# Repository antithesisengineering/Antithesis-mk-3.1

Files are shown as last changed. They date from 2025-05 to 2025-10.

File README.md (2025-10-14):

# Antithesis MK3 & MK3.1

[**Build Guide**](https://download-directory.github.io/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)

Printed Parts [**HERE**](https://download-directory.github.io/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)

Bill Of Materials [**HERE**](BOM/Antithesis_MK3.1_BOM_REV1.csv)

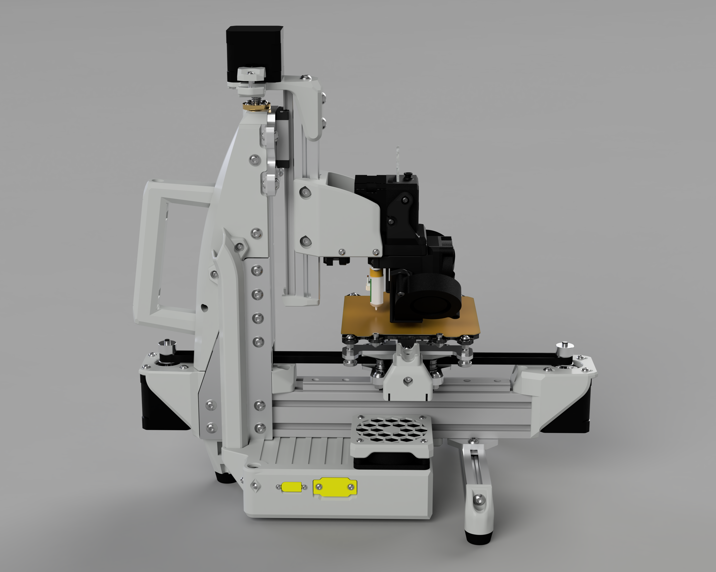
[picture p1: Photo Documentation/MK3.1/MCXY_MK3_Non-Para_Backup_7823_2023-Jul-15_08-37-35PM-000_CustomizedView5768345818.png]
printer pic


## Specifications for MK3.1/MK3
-Build Area XYZ: 13x10x10cm (5⅛ x 4 x 4 in)/10x10x10cm (4 x 4 x 4 in)

-Basic Size H W L: 384 x 245 x 395 mm (15⅛ x 9⅝ x 15½ in)

-Axes Extended Size H W L: 489 x 351 x 395 mm (19¼ x 13⅞ x 15½ in)

-Printer Weight: 5kg (11lbs)
-Gantry Weight: 630g (1.4lbs)

-Shaper Frequency X Y: 66Hz/75HZ 72Hz/72Hz

-Power Printing: 80W
-Power Max: 200W

-Advised Max: 15K mm/s² @ 500mm/s, 40K mm/s² @ 300mm/s
-Absolute Max: 20K mm/s² @ 500mm/s, 100K mm/s² @ 300mm/s

## Components
-MCU: Manta M5P/SKR Pico

-Host: CB2/CB1

-Extruder: Orbiter V2.5/LGX Pro/LGX Lite V2 

-Hotend: Phaetus Conch Plus/Mosquito Magnum/More to come

-Probe: BL Touch

-Part Cooling: x2 5015 or x2 7530 Blower Fans

-Bed Heater: 10x13cm V0.1 PCB Heater/10x10cm Keenovo 24V

-Stepper Drivers: TMC2209/TMC5160T Pro

-XY Steppers: 42STH48-1684MAC/42STH48-2504AC - Speedy Power

-Z Stepper: 42STH40-1684L300E

## HUGE thanks to the following
[**Killa_Prints**](https://www.youtube.com/@Killa_Prints)

[**FSMMeatball**]

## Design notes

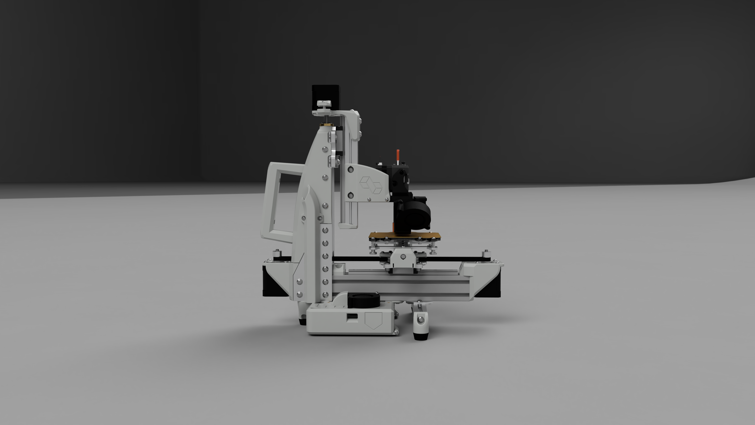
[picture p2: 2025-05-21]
Photo Documentation/MK3/MCXY_MK3_Para_2023-Apr-03_12-15-32PM-000_CustomizedView17845813854.png

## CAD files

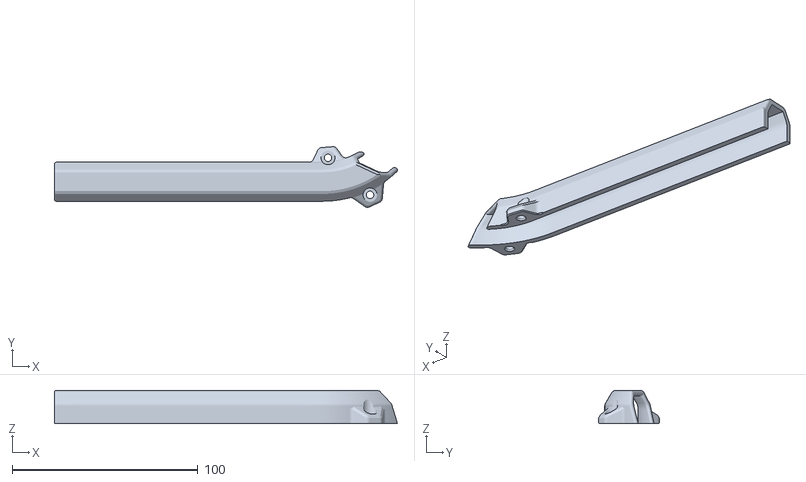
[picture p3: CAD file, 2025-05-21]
STLS/Controllers/Manta M5P/Main Cable Conduit.stl
184.4 x 32.7 x 18.0

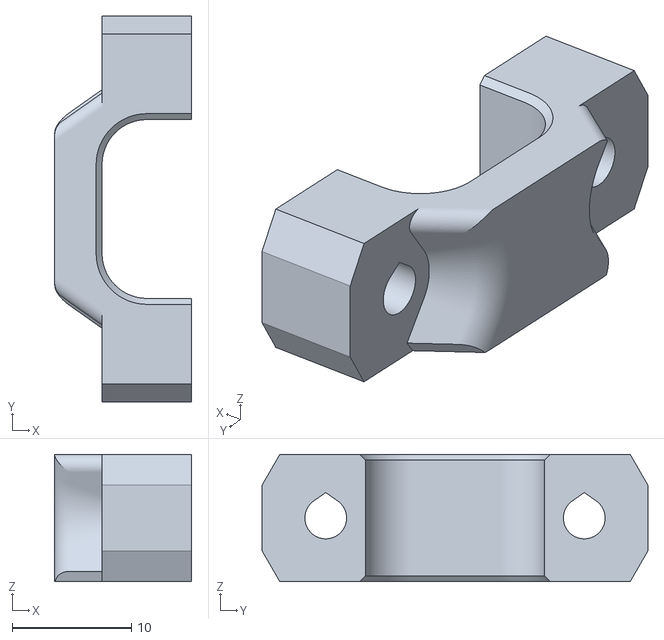
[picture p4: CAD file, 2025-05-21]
STLS/Controllers/Manta M5P/Enclosure Main Cable Clamp.stl
11.5 x 32.4 x 10.7

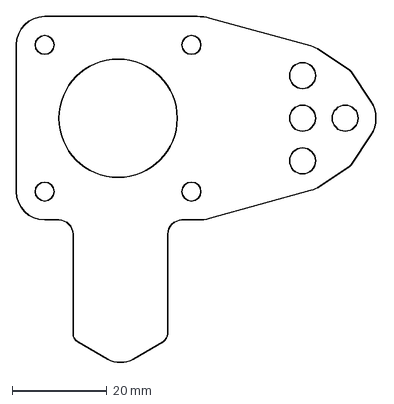
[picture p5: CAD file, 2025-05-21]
Send Cut Send DXF/Sheet Cut Parts/Z Motor Mount.dxf
76.4 x 73.3 mm

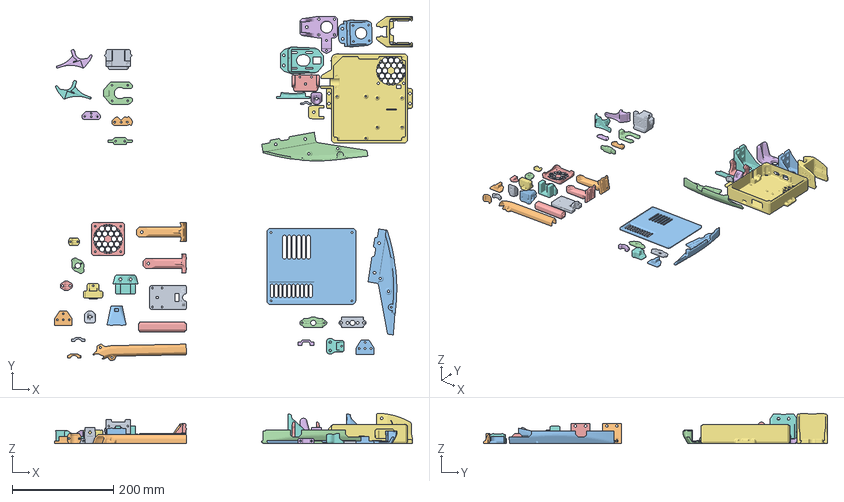
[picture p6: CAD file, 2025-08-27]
STLS/Antithesis MK3.1 - Mellow DP5.3mf
707.0 x 679.2 x 60.0 mm
Mosquito Hotend Adapter
Lower Handle Mount
Left Cover
Belt Tensioner
Upper Handle Mount
Part Cooling Fan Mount
Printhead Mount
Part Cooling Fan Mount M
Printhead Modular Plate
Bed Cable Cover Bottom
MCU Enclosure Lid
BL Touch Probe Mount
Handle Grip
Bed Cable Cover Top
MCU Enclosure
Endstop
WobbleX Mount Bottom
Main Cable Conduit
Rear Foot Mount
WobbleX Mount Top
Enclosure Fan Shroud
Plastic Z Motor Mount
X Axis Belt Block
X Axis Idler Mount
Foot Mount x 2
Carriage Idler Mount x 2
WobbleX Lead Screw Nut Mount
Bed Cable Clamp
Enclosure Main Cable Clamp
Bed Cable Clamp Bottom
Front Stepper Mount
Printhead Cable Mount
Z Axis Cable Clamp
Rear Stepper Mount
Right Cover
LGX Extruder Adapter
Z Axis Endstop
PTFE Tube Mount
Bed Cable Clamp Top

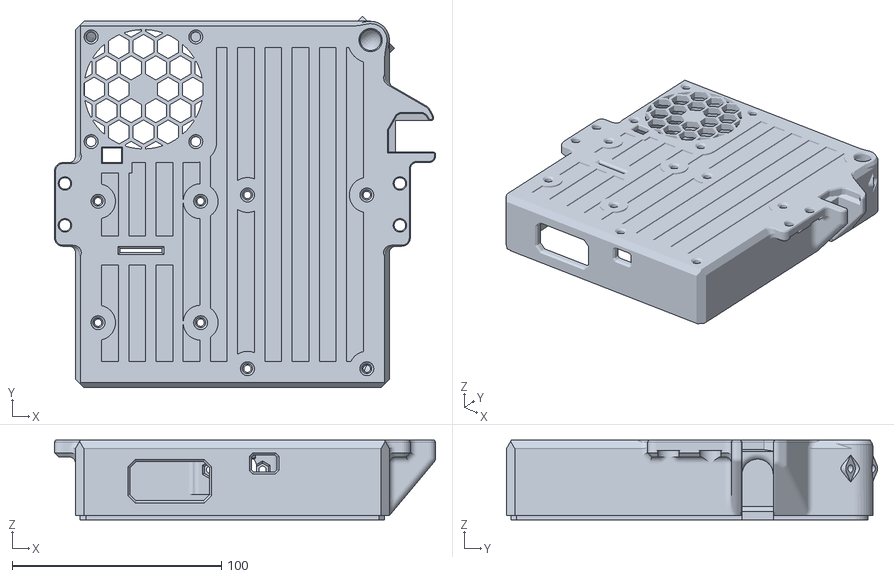
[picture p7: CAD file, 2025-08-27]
STLS/Controllers/Mellow D5/D5 - MCU Enclosure.stl
182.0 x 177.3 x 38.0

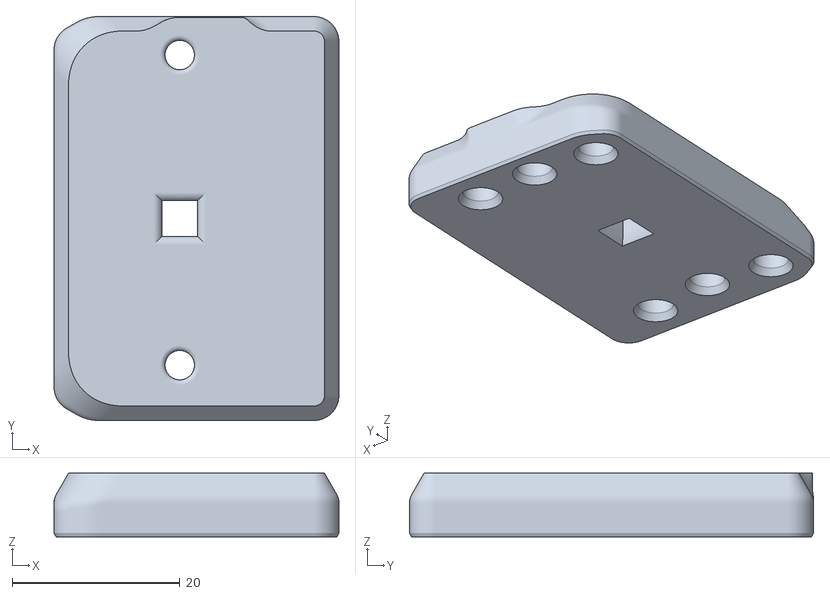
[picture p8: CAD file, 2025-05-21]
STLS/Extruder Adapters/Orbiter V2.5 Extruder Adapter.stl
34.0 x 48.2 x 7.60

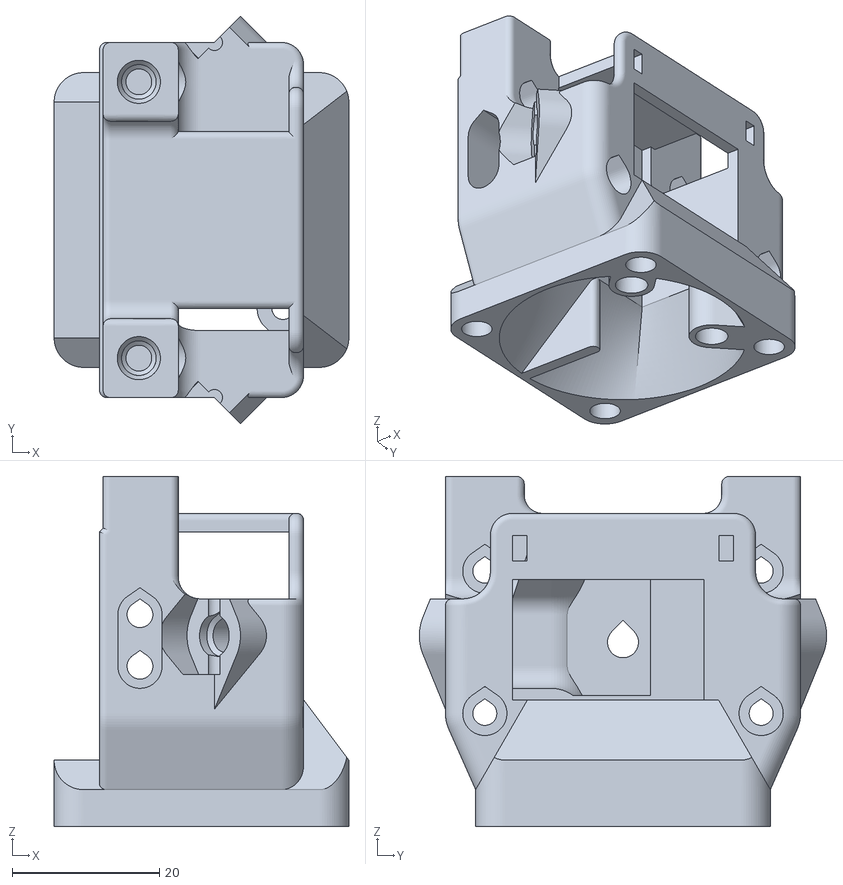
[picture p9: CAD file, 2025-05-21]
STLS/Hotend Adapters/Bambu Style/Phaetus Conch Hotend Adapter.stl
40.0 x 55.3 x 47.5

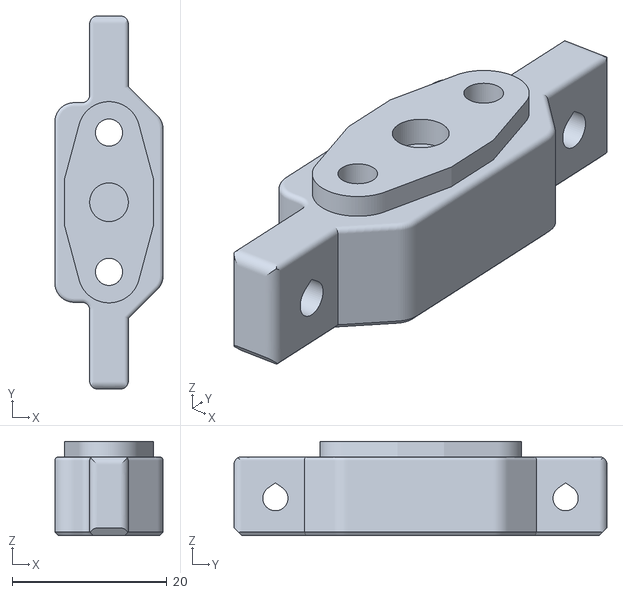
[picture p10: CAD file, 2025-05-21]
STLS/Hotend Adapters/Mosquito/BL Touch Probe Mount.stl
14.0 x 48.2 x 12.2

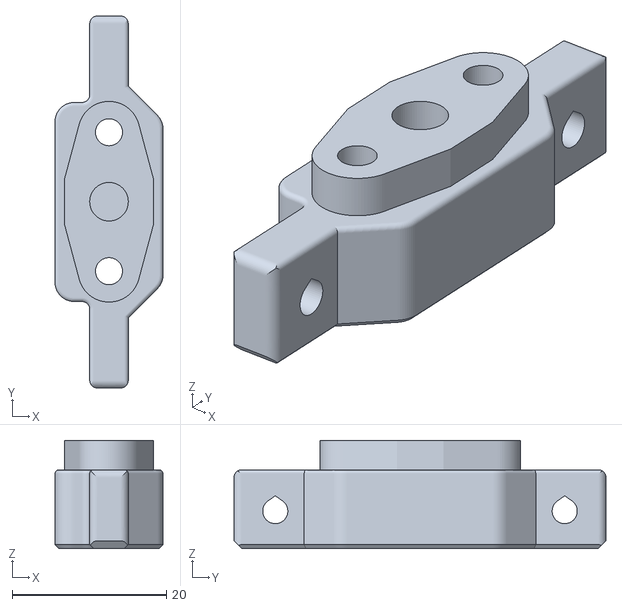
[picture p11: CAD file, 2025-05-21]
STLS/Hotend Adapters/Revo/BL Touch Probe Mount.stl
14.0 x 48.2 x 14.0

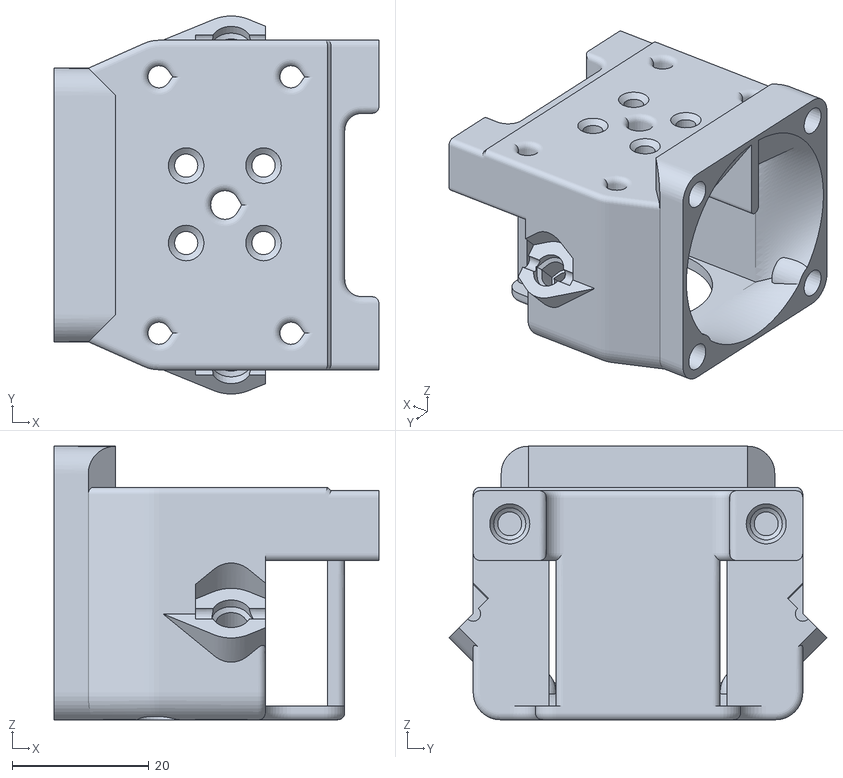
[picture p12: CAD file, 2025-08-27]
STLS/Hotend Adapters/Teakettle/Teakettle Hotend Adapter.stl
47.5 x 55.3 x 40.0

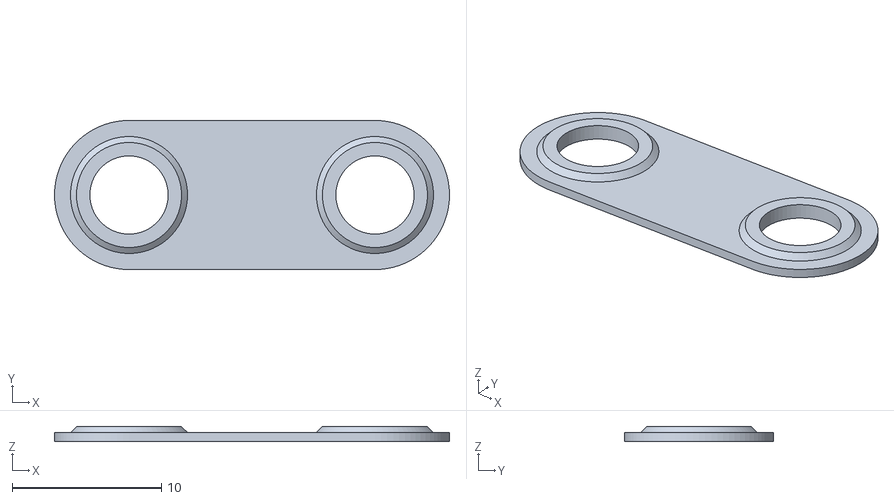
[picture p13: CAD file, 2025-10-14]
STLS/Main/X Axis Idler Shim.stl
26.5 x 10.0 x 1.00

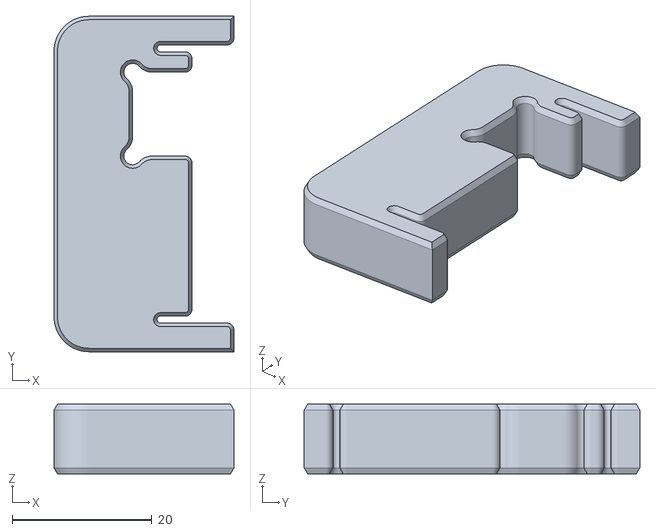
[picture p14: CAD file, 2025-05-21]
STLS/Printable Build Assistance Devices/MGN12-4040 Rail Alignment Tool.stl
25.8 x 48.0 x 10.0

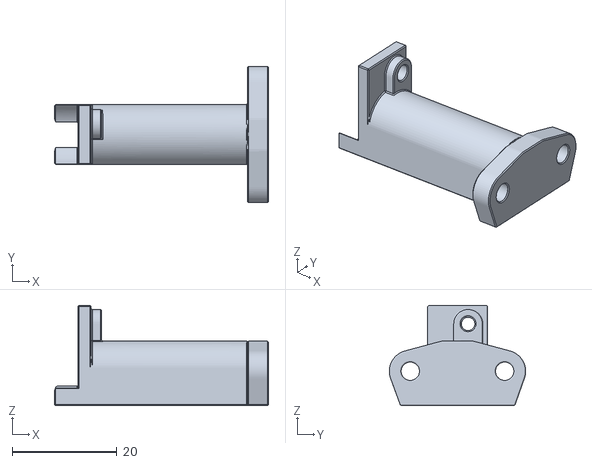
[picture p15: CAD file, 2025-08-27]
STLS/Probe Adapters/Thick_Mount_BDsensor_42mm.stl
40.8 x 26.0 x 19.1

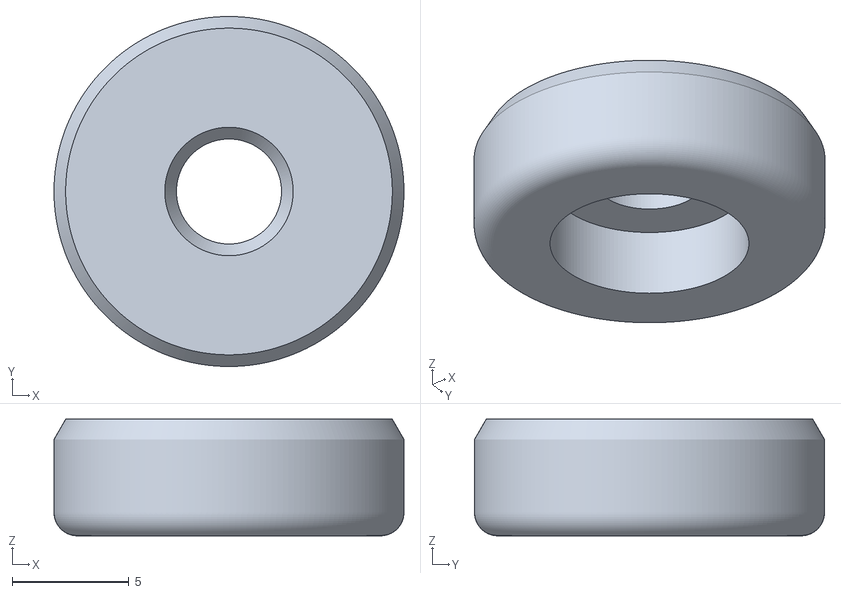
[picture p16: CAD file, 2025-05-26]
STLS/PSU Case/Power Supply Foot Short.stl
15.0 x 15.0 x 5.00

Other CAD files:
User mods/Killa_Prints/KP LED Duct Mount V1_6.step
User mods/Killa_Prints/LGX/LGX - NH36 Mount.step
Send Cut Send DXF/Sheet Cut Parts/Foot Bracket.dxf
STLS/Controllers/Manta M5P/Bed Cable Clamp.stl
STLS/Controllers/Manta M5P/Enclosure Fan Shroud.stl
STLS/Controllers/Manta M5P/MCU Enclosure Lid.stl
STLS/Controllers/Manta M5P/MCU Enclosure with 48V Connector.stl
STLS/Extruder Adapters/LGX Extruder Adapter.stl
STLS/Hotend Adapters/Bambu Style/BL Touch Probe Mount.stl
STLS/Hotend Adapters/Bambu Style/Part Cooling Fan Mount M.stl
STLS/Hotend Adapters/Bambu Style/Part Cooling Fan Mount.stl
STLS/Hotend Adapters/Mosquito/Mosquito Hotend Adapter.stl
STLS/Hotend Adapters/Mosquito/Part Cooling Fan Mount M.stl
STLS/Hotend Adapters/Mosquito/Part Cooling Fan Mount.stl
STLS/Hotend Adapters/Revo/Part Cooling Fan Mount M.stl
STLS/Hotend Adapters/Revo/Part Cooling Fan Mount.stl
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

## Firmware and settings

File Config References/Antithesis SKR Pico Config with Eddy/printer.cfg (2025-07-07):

[include mainsail.cfg]
# This file contains common pin mappings for the BIGTREETECH SKR Pico V1.0
# To use this config, the firmware should be compiled for the RP2040 with
# USB communication.

# The "make flash" command does not work on the SKR Pico V1.0. Instead,
# after running "make", copy the generated "out/klipper.uf2" file
# to the mass storage device in RP2040 boot mode

## Voron Design VORON 0.2 SKR Pico V1.0 config

## *** THINGS TO CHANGE/CHECK: ***
## MCU path                                                                     [mcu] section
## Z and Extruder motor currents                                                [tmc2209 stepper_*] sections. Uncomment the stepper motor you have
## Full steps per rotation for Extruder                                         [extruder] section
## Thermistor types                                                             [extruder] and [heater_bed] sections - See https://www.klipper3d.org/Config_Reference.html#common-thermistors for common thermistor types
## Motor currents                                                               [extruder] [stepper] and [_HOME_X/Y] macro sections
## PID tune                                                                     [extruder] and [heater_bed] sections
## Fine tune E steps                                                            [extruder] section
## For more info                                                                check https://docs.vorondesign.com/build/startup/#v0

[mcu]
#####################################################################
# Obtain definition by "ls -l /dev/serial/by-id/"
#####################################################################
##serial: /dev/serial/by-id/usb-Klipper_rp2040_50445061205AE01C-if00
serial: /dev/ttyAMA0 											# for UART connection
baud: 250000
restart_method: command

[mcu eddy]
serial: /dev/serial/by-id/usb-Klipper_rp2040_45474E621B02D69A-if00 
restart_method: command


[force_move]
enable_force_move: true

[temperature_sensor mcu_temp]
sensor_type: temperature_mcu
min_temp: 0
max_temp: 100

[temperature_sensor raspberry_pi]
sensor_type: temperature_host
min_temp: 10
max_temp: 100

[temperature_sensor btt_eddy_mcu]
sensor_type: temperature_mcu # Sets the type of sensor for Klipper to read
sensor_mcu: eddy # Sets the MCU of the eddy probe tempereature sensor
min_temp: 10 # Sets the minimum tempereature for eddys tempereature sensor to operate
max_temp: 100 # Sets the maximum tempereature for eddys tempereature sensor to operate

[probe_eddy_current btt_eddy]
sensor_type: ldc1612
z_offset: 1.5
#i2c_address:
i2c_mcu: eddy  # This value is good for the Eddy USB but would need to be adjusted for the Eddy Coil according to the MCU you have used.
i2c_bus: i2c0f # This value is good for the Eddy USB but would need to be adjusted for the Eddy Coil according to the I2C bus you have used.
# Measure the offsets below using the method described here: https://www.klipper3d.org/Probe_Calibrate.html#calibrating-probe-x-and-y-offsets
# For a standard Voron stealthburner X carriage mount there should be no need to change the defaults below.
x_offset: 0
y_offset: 24

# This section is only relevant for Eddy USB. Comment it out for Eddy Coil.
[temperature_probe btt_eddy]
sensor_type: Generic 3950
sensor_pin: eddy:gpio26
horizontal_move_z: 2

[bed_mesh]
horizontal_move_z: 4
speed: 200
mesh_min: 20,20
mesh_max: 120,100

[printer]
kinematics: corexy
max_velocity: 200
max_accel: 2000
max_z_velocity: 15
max_z_accel: 300
square_corner_velocity: 6.0

#####################################################################
#      X/Y Stepper Settings
#####################################################################

[stepper_x]         #Antithesis Back Stepper 
step_pin: gpio11
dir_pin: !gpio10                                           # Check motor direction in link above. If inverted, add a ! before gpio10
enable_pin: !gpio12
endstop_pin: tmc2209_stepper_x:virtual_endstop
rotation_distance: 40
microsteps: 32
full_steps_per_rotation: 200                               # Set to 400 for 0.9° degree stepper motor, 200 is for 1.8° stepper motors
endstop_pin: tmc2209_stepper_x:virtual_endstop
position_endstop: 0
#position_min: -1
position_max: 130
homing_speed: 30
homing_retract_dist: 0
#homing_positive_dir: false


[tmc2209 stepper_x]
uart_pin: gpio9
tx_pin: gpio8
uart_address: 0
interpolate: False
run_current: 1.06
#hold_current: 0
# you need to calculate the run_current value using the equation (rated_motor_current * 0.707 = Maximum_run_current) start with a value that is about 60%-70% of your maximum value.
sense_resistor: 0.110
stealthchop_threshold: 0                                            # Set to 999999 to turn stealthchop on, and 0 to use spreadcycle
diag_pin: ^gpio4    												# YOU NEED TO JUMP THIS DIAG PIN ON YOUR BOARD FOR SENSORLESS HOMING TO WORK 
driver_SGTHRS: 80  												# this is set to 255 which is the MAX sensitivity for sensorless homing, you will need to tune this later

[stepper_y]         #Antithesis Front Stepper 
step_pin: gpio6
dir_pin: gpio5                                                      # Check motor direction in link above. If inverted, add a ! before gpio5
enable_pin: !gpio7
endstop_pin: tmc2209_stepper_y:virtual_endstop
rotation_distance: 40
microsteps: 32
full_steps_per_rotation: 200                                        # Set to 400 for 0.9° degree stepper motor, 200 is for 1.8° stepper motors
endstop_pin: tmc2209_stepper_y:virtual_endstop
position_endstop: 0
position_max: 105
homing_speed: 30
homing_retract_dist: 0
#homing_positive_dir: false

[tmc2209 stepper_y]
uart_pin: gpio9
tx_pin: gpio8
uart_address: 2
interpolate: False
run_current: 1.06
#hold_current: 0
# you need to calculate the run_current value using the equation (rated_motor_current * 0.707 = Maximum_run_current) start with a value that is about 60%-70% of your maximum value.
sense_resistor: 0.110
stealthchop_threshold: 0                                            # Set to 999999 to turn stealthchop on, and 0 to use spreadcycle
diag_pin: ^gpio3    												# YOU NEED TO JUMP THIS DIAG PIN ON YOUR BOARD FOR SENSORLESS HOMING TO WORK 
driver_SGTHRS: 80  												# this is set to 255 which is the MAX sensitivity for sensorless homing, you will need to tune this later

#####################################################################
#   Z Stepper Settings
#####################################################################

[stepper_z]
step_pin: gpio19
dir_pin: gpio28                                                    # Remove the ! before gpio28 if motor direction is inverted.
enable_pin: !gpio2
rotation_distance: 8                                                # For T8x8 integrated lead screw
microsteps: 32
#endstop_pin: ^gpio25    
endstop_pin: probe:z_virtual_endstop
#position_endstop: 0    comment for eddy
position_max: 120
position_min: -2       #default was -1.5
homing_speed: 20
second_homing_speed: 3.0
homing_retract_dist: 3.0
homing_positive_dir: false

[tmc2209 stepper_z]
uart_pin: gpio9
tx_pin: gpio8
uart_address: 1
interpolate: False
## For OMC (StepperOnline) 17LS13-0404E-200G 0.4A 
run_current: 1.06
## For LDO-42STH25-1004CL200E 1.0A
#run_current: 0.37
sense_resistor: 0.110
stealthchop_threshold: 0                                            # Set to 999999 to turn stealthchop on, and 0 to use spreadcycle

#####################################################################
#   Extruder
#####################################################################

[extruder]
step_pin: gpio14
dir_pin: gpio13                                                     # Add ! if moving opposite direction
enable_pin: !gpio15
full_steps_per_rotation: 200                                       # Set to 200 for LDO 1.8° stepper motor, and set to 400 for OMC(StepperOnline) 0.9° stepper motor
rotation_distance: 5.586                                           # See calibrating rotation_distance on extruders doc Default 5.7
#gear_ratio: 50:10                                                   # For Mini Afterburner
microsteps: 32
nozzle_diameter: 0.400
filament_diameter: 1.750
heater_pin: gpio23
## Check what thermistor type you have. See https://www.klipper3d.org/Config_Reference.html#common-thermistors for common thermistor types.
## Use "Generic 3950" for NTC 100k 3950 thermistors
sensor_type: Generic 3950
sensor_pin: gpio27
#control: pid                                                        # Do PID calibration after initial checks
#pid_Kp: 28.182
#pid_Ki: 1.978
#pid_Kd: 100.397
min_temp: 0
max_temp: 270
min_extrude_temp: 150
max_extrude_only_distance: 150
max_extrude_cross_section: 0.8
pressure_advance: 0.045                                               # See tuning pressure advance doc
pressure_advance_smooth_time: 0.040
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

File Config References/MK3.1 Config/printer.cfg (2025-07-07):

# Config is for a Antithesis MK3.1 with a BTT Manta M5P and CB2 #

[include mainsail.cfg]
#[include ADXL345.cfg]



[mcu]
serial: /dev/serial/by-id/usb-Klipper_stm32g0b1xx_2F001E000C504B5735313920-if00



[printer]
kinematics: corexy
max_velocity: 500
max_accel: 20000
minimum_cruise_ratio: 0
max_z_velocity: 15
max_z_accel: 100
square_corner_velocity: 5



[stepper_x]
step_pin: PC8
dir_pin: !PC9
enable_pin: !PA15
endstop_pin: tmc2209_stepper_x:virtual_endstop
microsteps: 32
rotation_distance: 40
full_steps_per_rotation: 400
position_endstop: -2.5
position_min: -2.5
position_max: 130
homing_retract_dist: 0
homing_speed: 40

[tmc2209 stepper_x]
uart_pin: PD9
diag_pin: ^PD3
driver_SGTHRS: 150
sense_resistor: 0.110
run_current: 1.1
interpolate: False
stealthchop_threshold: 0



[stepper_y]
step_pin: PA10
dir_pin: PA14
enable_pin: !PA13
endstop_pin: tmc2209_stepper_y:virtual_endstop
microsteps: 32
rotation_distance: 40
full_steps_per_rotation: 400
position_endstop: -5
position_min: -5
position_max: 100
homing_retract_dist: 0
homing_speed: 40

[tmc2209 stepper_y]
uart_pin: PD8
diag_pin: ^PD2
driver_SGTHRS: 150
sense_resistor: 0.110
run_current: 1.1
interpolate: False
stealthchop_threshold: 0



[stepper_z]
step_pin: PC6
dir_pin: PC7
enable_pin: !PA9
endstop_pin: probe:z_virtual_endstop
microsteps: 32
rotation_distance: 4
full_steps_per_rotation: 200
position_min: -1
position_max: 102.5
homing_retract_dist: 5
homing_speed: 5

[tmc2209 stepper_z]
uart_pin: PB10
#diag_pin: PC3
sense_resistor: 0.110
run_current: 1.0
interpolate: False
stealthchop_threshold: 0



[extruder]
step_pin: PB12
dir_pin: PB11
enable_pin: !PA8
heater_pin: PC5
sensor_pin: PA1
sensor_type: Generic 3950
control: pid
pid_Kp: 43.862
pid_Ki: 17.201
pid_Kd: 27.962
min_temp: 15
max_temp: 290
microsteps: 16
rotation_distance: 4.603
full_steps_per_rotation: 200
nozzle_diameter: 0.400
filament_diameter: 1.750
max_extrude_only_distance: 500
max_extrude_cross_section: 100
max_extrude_only_velocity: 120
pressure_advance: 0.04
pressure_advance_smooth_time: 0.03

[tmc2209 extruder]
uart_pin: PB2
#diag_pin: PC2
sense_resistor: 0.110
run_current: 0.85
interpolate: True
stealthchop_threshold: 0
driver_TBL: 0
driver_HEND: 6
driver_HSTRT: 7
driver_TOFF: 4



[heater_bed]
heater_pin: PA5
sensor_pin: PA0
sensor_type: Generic 3950
control: pid
pid_Kp: 58.249 
pid_Ki: 1.904 
pid_Kd: 445.608
min_temp: 15
max_temp: 105



[bltouch]
sensor_pin: PC13
control_pin: PC15
pin_move_time: 0.7
x_offset: 0
y_offset: 25
#z_offset: 2.21
speed: 5
lift_speed: 15
stow_on_each_sample: False



[bed_mesh]
speed: 250
horizontal_move_z: 5
mesh_min: 2.5, 21
mesh_max: 127.5, 97.5
probe_count: 5, 3
fade_start: 1.0
fade_end: 5.0



[fan]
pin: PA4
max_power: 1.0
shutdown_speed: 0
#cycle_time: 0.01
kick_start_time: 0.1
off_below: 0.15



[heater_fan heatbreak_cooling_fan]
pin: PA3
max_power:1.0
shutdown_speed: 1.0
heater: extruder
heater_temp: 50
fan_speed: 1.0



[homing_override]
axes: xyz
set_position_z: 0
gcode:   
    {% set HOME_ACC = 1000 %}   
    {% set CONFIG_ACC = printer.configfile.settings['printer'] %}
    {% set NORMAL_ACC = CONFIG_ACC.max_accel %}
    SET_VELOCITY_LIMIT ACCEL={HOME_ACC}
    SET_STEPPER_ENABLE STEPPER=stepper_x ENABLE=1
    SET_STEPPER_ENABLE STEPPER=stepper_y ENABLE=1
    G4 P2000
    G90
    G0 Z4 F900
    {% set HOME_CUR = 0.5 %}
    {% set CONFIG_CURX = printer.configfile.settings['tmc2209 stepper_x'] %}
    {% set NORMAL_CURX = CONFIG_CURX.run_current %}
    {% set CONFIG_CURY = printer.configfile.settings['tmc2209 stepper_y'] %}
    {% set NORMAL_CURY = CONFIG_CURY.run_current %}
    SET_TMC_CURRENT STEPPER=stepper_x CURRENT={HOME_CUR}
    SET_TMC_CURRENT STEPPER=stepper_y CURRENT={HOME_CUR}
    G4 P2000
    G28 Y0
    G90
    G1 Y0 F1200
    G4 P2000
    G28 X0
    G90
    G1 X0 F1200
    SET_TMC_CURRENT STEPPER=stepper_y CURRENT={NORMAL_CURY}
    SET_TMC_CURRENT STEPPER=stepper_x CURRENT={NORMAL_CURY}
    G4 P1000
    G0 X65 Y25 F6000
    G28 Z0
    G0 Z10 F900
    SET_VELOCITY_LIMIT ACCEL={NORMAL_ACC}



[input_shaper]
shaper_type_x = mzv
shaper_freq_x = 66.8
shaper_type_y = mzv
shaper_freq_y = 73.4



[gcode_macro TT]
gcode: 
    TUNING_TOWER COMMAND=M220 PARAMETER=S START=100 STEP_DELTA=100 STEP_HEIGHT=2



[gcode_macro _CLIENT_VARIABLE]
variable_use_custom_pos   : True ; #use custom park coordinates for x,y [True/False]
variable_custom_park_x    : 65.0   ; #custom x position; value must be within your defined min and max of X
variable_custom_park_y    : 100.0   ; #custom y position; value must be within your defined min and max of Y
variable_custom_park_dz   : 2.0   ; #custom dz value; the value in mm to lift the nozzle when move to park position
variable_retract          : 1.0   ; #the value to retract while PAUSE
variable_cancel_retract   : 5.0   ; #the value to retract while CANCEL_PRINT
variable_speed_retract    : 35.0  ; #retract speed in mm/s
variable_unretract        : 1.0   ; #the value to unretract while RESUME
variable_speed_unretract  : 35.0  ; #unretract speed in mm/s
variable_speed_hop        : 15.0  ; #z move speed in mm/s
variable_speed_move       : 100.0 ; #move speed in mm/s
variable_park_at_cancel   : True ; #allow to move the toolhead to park while execute CANCEL_PRINT [True/False]
variable_park_at_cancel_x : None  ; #different park position during CANCEL_PRINT [None/Position as Float]; park_at_cancel must be True
variable_park_at_cancel_y : None  ; #different park position during CANCEL_PRINT [None/Position as Float]; park_at_cancel must be True
## !!! Caution [firmware_retraction] must be defined in the printer.cfg if you set use_fw_retract: True !!!
variable_use_fw_retract   : False ; #use fw_retraction instead of the manual version [True/False]
variable_idle_timeout     : 0     ; #time in sec until idle_timeout kicks in. Value 0 means that no value will be set or restored
gcode:

[include moonraker_obico_macros.cfg]

#*# <---------------------- SAVE_CONFIG ---------------------->
#*# DO NOT EDIT THIS BLOCK OR BELOW. The contents are auto-generated.
#*#
#*# [extruder]
#*#
#*# [bltouch]
#*# z_offset = 2.370
#*#
#*# [bed_mesh default]
#*# version = 1
#*# points =
#*# 	  0.097500, 0.066250, 0.038750, 0.079375, 0.098750
#*# 	  0.058125, 0.102500, 0.045625, 0.103750, 0.100000
#*# 	  0.067500, 0.020000, -0.015000, 0.000625, 0.042500
#*# x_count = 5
#*# y_count = 3
#*# mesh_x_pps = 2
#*# mesh_y_pps = 2
#*# algo = lagrange
#*# tension = 0.2
#*# min_x = 2.5
#*# max_x = 127.5
#*# min_y = 21.0
#*# max_y = 97.5

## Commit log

2025-05-21 Create Foot Bracket Alignment Tool.stl
    [Foot Bracket Alignment Tool.stl]
2025-05-21 Create MGN12-4040 Rail Alignment Tool.stl
    [MGN12-4040 Rail Alignment Tool.stl]
2025-05-22 3MF for all parts & Hotend stuff for Teakettle
    [Antithesis MK3.1 - KP Mods v12.3mf, BL Touch Probe Mount.stl, Part Cooling Fan Mount - Left.stl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]
2025-06-02 BOM upload
    [Antithesis MK3.1 BOM REV1.csv]
2025-06-14 Update Antithesis MK3.1 - KP Mods v12.3mf
    [Antithesis MK3.1 - KP Mods v12.3mf]
2025-06-15 Update Antithesis MK3.1 BOM REV1.csv
    [Antithesis MK3.1 BOM REV1.csv]
2025-06-20 All Parts for BambuStudio
    3MF file for BambuStudio. Electronics case is modified to use Mellow D5 Mainboard.
    [Antithesis MK3.1 - KP Mods v12.3mf, Antithesis MK3.1 - Mellow DP5.3mf]
2025-07-06 Add Sequins to Fan Ducts
    [D5 - MCU Enclosure.stl, LGX - EBB42 - Mount v7.stl, Part Cooling Fan Mount Left_Sequin.stl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]
2025-07-06 Create XT60E-F Blockoff Plate.stl
    [XT60E-F Blockoff Plate.stl]
2025-07-13 file updates
    [LGX - NH36 Mount.stl]
2025-07-14 Updated fan ducts and NH36 to LGX mount
    [KP LED Duct Mount V1_6.step, LGX - EBB42 - Mount v7.stl, LGX - NH36 Mount.step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]
2025-07-24 Update README.md
    Added extruder and main board options
2025-10-14 Rename BOM file and update link in README.md
    [Antithesis_MK3.1_BOM_REV1.csv, X Axis Idler Shim.stl]
